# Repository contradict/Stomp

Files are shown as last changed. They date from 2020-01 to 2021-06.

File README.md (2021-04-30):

# Software for the Pneumatic Legged Robot "Chomp"

This repository contains the control software for Chomp the BattleBot.
Presently, Chomp has two separate systems the Hull and the Turret. Each is
entirely self-contained with its own power and control systems. A rough
[schematic](SystemBlockDiagrams) of the Hull is available.

## Hull

The Hull consists of 6 leg modules. Each leg has a control [board](LegBoard) for
local joint coordination. This board uses an STM32F722 microcontroller to
communicate with the joint angle sensors, the Enfield S2 servos, and the central
microcontroller.  This processor measures the joint angles and provides
pneumatic cylinder length feedback as an analog voltage to the servos. Commands
are provided over an RS485 serial connection using the Modbus protocol and can
configure the servos, command a toe position, and provide status information
such as measured leg position and cylinder pressures.

The central microcontroller is a BeagleBone AI running Debian Linux. Two
executables are used during operation
[sbus_radio](Hull/HullControl/src/sbus_radio) reads serial data from a FrSky
receiver and emits a stream of data using [LCM](https://lcm-proj.github.io/).
[leg_control](Hull/HullControl/src/leg_control) listens to these messages and
passes them to a realtime
([SCHED_FIFO](https://man7.org/linux/man-pages/man7/sched.7.html)) thread. This
thread determines the desired toe positions and communicates with the legs over
the RS485 bus.

## Turret

The Turret uses the control electronics from the previous revision of
[Chomp](https://www.github.com/jascahlittle/Chomp). This uses a single Arduino
Mega with an ATMega2560 to switch the pneumatic valves for firing the hammer and
communicate with the control radio, turret rotation motor controller, LeddarTech
M16-LSR, and telemetry radio. There is a nice overview of the control software
[here](Turret/arduino/turret). This software handles the automatic tracking and
hammer firing using the ranging data from the LeddarTech M16-LSR, as well as
precisely scheduling the valve timings to ensure a clean throw and retract of
the hammer.

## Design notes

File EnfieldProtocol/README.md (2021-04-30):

# Enfield S3 Serial Protocol Documentation

## Introduction

This documentation is incomplete and generated by watching the communication
between the Enfield configuration tool and a valve. The USB connection is
converted to serial on the bottom of the two boards inside the servo, I connected
after this conversion as shown here:
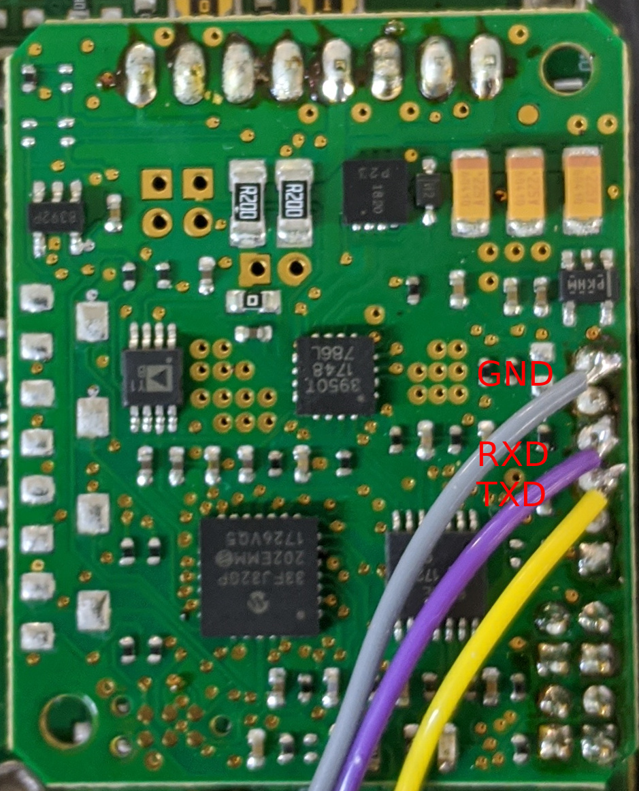
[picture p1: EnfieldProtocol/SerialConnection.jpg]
Serial Connection


To monitor communication, RXD and TXD were each connected to the Receive wire of
another serial port on a second laptop and `twocolumn.py` was used to monitor
the data flow while interacting with the tool. Once the protocol was clear,
`enfield.py` was written to send and receive messages.

## Wiring

In order to use this protocol, we modified our servos to have the following
connections. These colors are the colors in the cables we received from Enfield.

Pin | Color | Function
----------------------
 1  | BRN   | 24V
 2  | WHT   | Feedback Voltage
 3  | BLU   | GND
 4  | BLK   | TXD (data in to Enfield)
 5  | GRY   | RXD (data out of Enfield)

## The Protocol

Packets sent in both directions are fixed size and checksummed. All messages are
checksummed using the `modbus` CRC. Every valid packet produces a response, the
valve never sends an unrequested packet. Baud rate is 115200.

### Commands

Commands are sent to the valve and have the format

    $CrVV#CC

`r` identifies the target of the command and `VV` is a 16-bit payload. `CC` is
the CRC.

### Responses

Responses from the valve have the format

    +VV#CC

The returned 16 bit data is `VV`and the checksum is `CC`

### Observed Reads

The following `r` values return data about the valve and do not seem to affect
its operation. When reading, `VV` in the command packet is always set to 0x1111.
See the manual for a description of what each parameter means.

Name                | `r` |      | Range   | Description
--------------------|-----|------|---------|-------------
ProportionalGain    | 112 | 0x70 | 0-1000  | interpreted as 0-100.0%
DerivativeGain      | 113 | 0x71 | 0-1000  |
ForceDamping        | 119 | 0x77 | 0-1000  |
Offset              | 126 | 0x7E | 0-1000  |
CommandInput        | 127 | 0x7F | 0-1     |
FeedbackInput       | 128 | 0x80 | 0-1     |
AreaRatio           | 129 | 0x81 | 0-32767 | 32767 * (rod end piston area / bore area)
CylinderBore        | 130 | 0x82 | 0-32767 | 1024 * Cylinder Bore in inches
MinimumPosition     | 131 | 0x83 | 0-1000  |
MaximumPosition     | 132 | 0x84 | 0-1000  |
PortConnection      | 133 | 0x85 | 0-1     |
RampUp              | 134 | 0x86 | 0-1000  |
RampDown            | 135 | 0x87 | 0-1000  |
DeadBand            | 137 | 0x88 | 0-1000  |
DitherAmplitude     | 138 | 0x89 | 0-1000  |
ValveOffset         | 139 | 0x8A | 0-1000  |
Unknown             | 140 | 0x8B |         | response is 0x0000
FeedbackPolarity    | 144 | 0x90 | 0-1     |
DigitalCommand      | 145 | 0x91 | 0-4095  |
CommandSource       | 146 | 0x92 | 0-1     |
SerialNumberLo      | 147 | 0x93 |         | response is 0x79db
SerialNumberHi      | 148 | 0x94 |         | response is 0x0000
Unknown             | 149 | 0x95 |         | Only seen as first command, data is 0x2222 response is 0x0000
AnalogCommand       | 152 | 0x98 | 0-4095  | Read continuously by Enfield tool
FeedbackPosition    | 153 | 0x99 | 0-4095  | Read continuously by Enfield tool
BaseEndPressure     | 154 | 0x9A |         |
RodEndPressure      | 155 | 0x9B |         |
SpoolCurrentMeasured| 158 | 0x9E | 0-4096  | Idles at 2048
FirmwareVersionB    | 161 | 0xa1 | 0       | startup, response is 0000
FirmwareVersionA    | 162 | 0xa2 | 0       | startup, response is 0a00
FirmwareRevLow      | 163 | 0xa3 | 0       | startup, response is 3030
FirmwareRevHigh     | 164 | 0xa4 | 0       | startup, response is 4520 "33-0010-0000 E00"
Unknown             | 177 | 0xb1 | 0       | data 0x0000 on Enfield tool startup, response is 0xa00f
Unknown             | 185 | 0xb9 | 0       | data 0x0000 on Enfield tool startup, response is 0x0000

### Observed Writes

These operations change the state of the servo, but are not persisted across
power cycles until `SaveConfiguration` is sent.

Name              | 'r' | Range   | Description
------------------|-----|---------|------------
ProportionalGain  | 1   | 0-1000  |
DerivativeGain    | 2   | 0-1000  |
ForceDamping      | 8   | 0-1000  |
Offset            | 15  | 0-1000  |
CommandInput      | 16  | 0-1     | 0-4-20mA, 1-0-10v
FeedbackInput     | 17  | 0-1     | 0-4-20mA, 1-0-10v
AreaRatio         | 18  | 0-32767 | 32767 * (rod end piston area / bore area)
CylinderBore      | 19  | 0-32767 | 1024 * Cylinder Bore diameter in inches
MinimumPosition   | 20  | 0-1000  |
MaximumPosition   | 21  | 0-1000  |
PortConnection    | 22  | 0-1     | 0-standard, 1-transposed
RampUp            | 23  | 0-1000  |
RampDown          | 24  | 0-1000  |
DeadBand          | 26  | 0-1000  |
DitherAmplitude   | 27  | 0-1000  |
ValveOffset       | 28  | 0-1000  |
FeedbackPolarity  | 33  | 0-1     | 0-normal, 1-inverted
CommandSource     | 89  | 0-1     | 1-analog, 0-slider
DigitalCommand    | 88  | 0-4095  |
SetZeroGains      | 224 | 0       | always written 0 after changing command input type, no response also sent on 'reset to factory'
SaveConfiguration | 225 | 0       | write 0 to save configuration, no response

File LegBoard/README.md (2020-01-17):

# Stomp Leg Board

Each leg of the robot needs a control board to interface to the servos valves
and position sensors. The servos communicate with proprietary serial protocol
and the position sensors measure joint angle which needs to be converted to
cylinder length to use the built-in feedback loop.

## Board Layout

I added a representative connector for each connection this board will need and
picked a pinout. The layout of the connectors is being designed in parallel with
the rest of the leg, hopefully that will be settled soon. The pinout can be
freely changed, please update the Block Diagram schematic if it does.

## Electrical Specifications

## Power

Power is distrubeted from a central power distribution block on the robot
directly from a battery pack. The supplied voltage will be in the 18-28V range.
Each leg board will be supplied through a fuse at the distribution block.

### Enfield S2 servo valve output

| Signal | Description |
|---|---|
| Output Voltage | 24V nominal, the data sheet specs 10-28v |
| Output Current | 1A per valve |
| RXD | 5V TTL asynchronous serial data from servo valve |
| TXD | 5V TTL asynchronous serial data to servo valve |
| Feedback | 0-10V cylinder position measurement |

The feedback signal should have an analog bandwidth of at least 1kHz.

### Angular Position Sensor

| Signal | Description |
|---|---|
| +5V | Power to angle sensor, 10mA |
| Vsense | Measured angle, 0.25 to 4.75 over specified angle range |

The measurement circuit for Vsense should have at least 1kHz bandwidth.

### Communications Bus

The communication bus connects all the Leg Boards to the platform
microcontroller. The two connectors pass through A and B lines to make wiring
simple.

| Signal | Description |
|---|---|
| A | RS-485 A line |
| B | RS-485 B line |
| GND | Reference voltage for RS485 transcievers |
| Upstream | Connected to the Leg Board closer to the microcontroller or the |
| | microcontroller |
| Downstream | Connected to the Leg Board farter from the microcontroller |

I'm not sure how the grounding should work, it may be that ground should not be
wired in the harness on these connetors to avoid a ground loop, but I would like
to provide it in case we have signal integrity problems.

The `Upstream` and `Downstream` pins should each be connected to a processor
GPIO pin.  I would like to use them to avoid having to hard code addresses on
each board.

## Signal Processing

Since the position sensors we are installing measure angle and the servo valves
need to know cylinder length, each channela $i$  needs to calculate

```math
\theta_i =  as_i * (V_{sense} + ao_i)
l_{cylinder} = a_i + b_i \cos(\theta_i + \phi_i )
V_{feedback} = fo_i + fs_i * l_{cylinder}
```

Where $as_i$ and $ao_i$ define the conversion from sensor voltage to angle in
radians, $a_i$, $b_i$, and $phi_i$ define the geometry of the link, and $fo_i$
and $fs_i$ define the conversion from cylinder length back to voltage.

This calculation should take at most 20us per channel to ensure low latency and
CPU usage for the full calculation. This should not be hard for a
microcontroller with a clock rate of at least 50MHz.

## Communications Protocols

### Enfield S2

The processor will need to implement a serial port interface to the
Enfield S2 for delivering command positions and monitoring status. The
reverse-engineered protocol is described in the
[README](../../EnfieldProtocol/README.md). 

The pressure and feedback registers should be continously monitored while
sending the current position command.

### Leg Bus (RS-485)

The commnuication between the Platform microcontroller and the Leg Controllers
over the RS-485 bus should implement the MODBUS protocol.

TODO: MODBUS Register Map.

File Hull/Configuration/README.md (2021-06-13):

# BeagleBone AI setup notes

Comes from TI with account `debian:tempwd`, hostname beaglebone.

## Set debian password

    ssh debian@beaglebone
    passwd

## Packages

    sudo apt update && sudo apt upgrade
    sudo apt install gdb stow cmake \
        liblcm-dev liblcm-bin libglib2.0-dev \
        libtool-bin libbsd-dev \
        openjdk-8-jre libjchart2d-java liblcm-java

## Upgrade scripts

Must use `debian` account. Copied from [here](https://beagleboard.org/upgrade)

    cd /opt/scripts
    git pull
    sudo tools/update_kernel.sh

## Set hostname

The preferred hostname is `chomp-hull`

    sudo vim /etc/hostname

## User Account for developers

    sudo adduser <username>
    GRPS=$(groups | cut -d ' ' -f 2- | tr ' ' ',')
    sudo usermod -a -G $GRPS <username>

## Account for robot operation

    sudo adduser chomp
    GRPS=$(groups | cut -d ' ' -f 2- | tr ' ' ',')
    sudo usermod -a -G $GRPS <username>

## disable USB networking (don't need it, adds noise to the logs)

In `/etc/default/bb-boot`, add the line (or uncomment)

    USB_NETWORK_DISABLED=yes

In `/etc/network/interfaces`, comment out the whole `iface usb0` section.

In `/opt/scripts/boot/bbai.sh`, comment out the two blocks starting around line
368 that run `autocnifgure_usb[01].sh`.

## Ensure a multicast route always exists.
If LCM won't start at boot, this is probably the solution.

Add these two `post-up` lines to `/etc/network/interfaces`. The reset should
already be there:

    auto lo
    iface lo inet loopback
      post-up ifconfig lo multicast || true
      post-up route add -net 224.0.0.0 netmask 240.0.0.0 dev lo || true

## Reboot

If the kernel was upgraded above, a reboot is necessary before building the
devicetree overlays.

## Use new account

Unless you reboot, still has `beaglebone` hostname.

    exit
    ssh-copy-id <username>@beaglebone

Enter password, then ssh in with keys.

## Custom Devicetree

Builds custom device tree overlays for UART3, UART5, UART10, SPI3, ADC, and I2C
IMU. This should use your developer account.

    cd ~
    mkdir src
    cd src
    git clone git@github.com:contradict/BeagleBoard-DeviceTrees
    cd BeagleBoard-DeviceTrees
    git checkout -b chomp
    make

This command creates the file

    src/arm/BBAI-chompcape.dtb

Need to copy the file to `/lib/firmware/`

    sudo cp src/arm/BBAI-*.dtb /lib/firmware

## Config files

`uEnv.txt` needs to be updated, the lines at the end installing the DTB overlays
are the important part, be sure not to overwrite any kernel version parameters
earlier in the file.

    90-mikrobus-cape.rules -> /etc/udev/rules.d/

## Reboot

Again. To use the new dtb overlays.

    sudo reboot

## Fetch and build libmodbus

The version in the debian repositories is old and busted. The version from the
official libmodbus site works, but is missing diagnostics. For our branch with a
minimal diagnostics client, use this:

    cd src
    git clone -b diagnostics_client https://github.com/contradict/libmodbus
    cd libmodbus
    ./autogen.sh
    ./configure --prefix=/usr/local/
    make
    sudo make install DESTDIR=/usr/local/stow/libmodbus-diag
    sudo mv /usr/local/stow/libmodbus-diag/usr/local/* /usr/local/stow/libmodbus-diag
    sudo rm -r /usr/local/stow/libmodbus-diag/usr
    sudo stow -d /usr/local/stow libmodbus-diag

## Fetch and build project

    cd src
    git clone git@github.com:contradict/Stomp
    cd Stomp/Platform
    make -C Test
    make -C SimpleGait

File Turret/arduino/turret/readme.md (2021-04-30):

# Table Of Contents <!-- omit in toc --> #

- [Design Overview](#design-overview)
- [Controller Hierarchy](#controller-hierarchy)
- [Main Program (turret.ino)](#main-program-turretino)
- [State Machine Pattern](#state-machine-pattern)
- [Controller Pattern](#controller-pattern)
- [Notes about changes to original Chomp code](#notes-about-changes-to-original-chomp-code)

# Design Overview #

Most logic is implemented c++ classes that use the Chomp controller pattern ([see below](#controller-pattern)).  Each controller implements a state machine ([see state machine pattern below](#state-machine-pattern)).

There are 4 global controllers

- Turret Controller
- Target Tracking Controller
- Radio Controller
- Telemetry Controller

Each of these are a global instances and they are all declared in turret.ino.  Then an <code>extern</code> deceleration is provided in each of those controller's class header file.

The Turret Controller and the TargetTrackingController will consturct new private instances of the controller types they need to do thier job.  However, each of these private controllers are owned by a global controller, which should not expose access to those controllers.

# Controller Hierarchy #

The current controller hierachy looks like this

    Global Objects                Sub Objects (instantiated in global object init())
    --------------                --------------------------------------------------

    TurretController -------------+--- TurretRotationController --------+--- AutoAimController
                                  |
                                  +--- HammerController
                                  |
                                  +--- FlameThrowerController
                                  |
                                  +--- IMUController
                                  |
                                  + --- AutoFireController

    TargetTrackingController -----+--- TargetAcquisitionController ------+--- LeddarController

    RadioController

    TelemetryController

# Main Program (turret.ino) #

The main Arduino file is turret.ino.  This file is where the 4 global controllers are declared.

    TurretController Turret;
    TargetTrackingController TargetTracking;
    RadioController Radio;
    TelemetryController Telem;

In the <code>setup()</code> method, that is called when the Arduino is (re)started, the <code>Init()</code> method of the 4 global controllers is called to get everything started.  Then the <code>RestoreParas()</code> call is issed to the global controllers

    void setup()
    {
        Telem.Init();
        Radio.Init();
        TargetTracking.Init();
        Turret.Init();

        Telem.RestoreParams();
        TargetTracking.RestoreParams();
        Turret.RestoreParams();
    }

Then each update that the Arduino issues by calling <code>loop()</code> will call the <code>Update()</code> method on each of the 4 global controllers.

    void loop()
    {
        Radio.Update();
        TargetTracking.Update();
        Turret.Update();
        Telem.Update();
    }

# State Machine Pattern #

Each controller will define its states in an <code>enum</code> in the header file.  For example this is what the flameThrowerController defines:

    enum controllerState 
    {
        EInit,
        ESafe,
        
        EDisabled,
        EReadyToFire,

        EPulseFlameOn,
        EManualFlameOn,
 
        EInvalid = -1
    };

The state machine pattern used by all controllers basically consists of code in the main <code>Init()</code> method, the <code>Update()</code> method and a private <code>setState(controllerState p_state)</code> method.

The <code>Init()</code> method will ensure the state is set and initialize the <code>m_lastUpdateTime</code> private member variable.  Finally, the state will be set to the initial state, which should be name <code>EInit</code>.  All other initilization should happen in the code triggered by transitioning into the <code>EInit</code> state.

    void FlameThrowerController::Init()
    {
        m_state = EInvalid;    
        m_lastUpdateTime = micros();

        setState(EInit);
    }

The <code>Update()</code> will first do any update calculations needed to detect state transitions, then the current state of the controller is stablized by running through all valid state transitions.  Once the state has stablized, then any other update code can run.

    void FlameThrowerController::Update()
    {
        m_lastUpdateTime = micros();

        //  Do any processing necessary for being able to detect state transitions

        ...

        //  Stabilize our state

        while(true)
        {
            controllerState prevState = m_state;

            switch (m_state)
            {
                case EInit:
                {
                    setState(ESafe);
                }
                break;

                case ESafe:
                {
                    //  Stay in safe mode for a minimum of k_safeStateMinDt

                    if (m_lastUpdateTime - m_stateStartTime > k_safeStateMinDt && Radio.IsNominal())
                    {
                        setState(EDisabled);
                    }
                }
                break;

                case EDisabled:
                {
                    if (!Radio.IsNominal())
                    {
                        setState(ESafe);
                    }
                    else if (Radio.IsFlameEnabled() || Radio.IsFlamePulseEnabled())
                    {
                        setState(EReadyToFire);
                    }
                }
                break;

                ...

                default:
                break;
            }

            //  No more state changes, move on
            
            if (m_state == prevState)
            {
                break;
            }
        }

        //  Now that the state is stable, perform any other update processing

        ...
    }

# Controller Pattern #

# LEDDAR Processing Overview #

The [LEDDAR M16](https://leddartech.com/lidar/m16-multi-segment-sensor-module/)
produces 16 range measurements spread over a 48° horizontal by 3° vertical fan.
It is possible for each measurement to return multiple reflections, we accept
the one closest to the robot in each segment. The list of measurements is scanned,
looking for features that project radially inwards toward the robot, with some
careful handling of [edge
cases](https://github.com/contradict/Stomp/blob/f4baf6cf64f448c69cff76d400e4cbb2790b86ec/Turret/arduino/turret/targetAcquisitionController.cpp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).
These segmentations are then compared to the current state of an
[$\alpha-\beta$](https://en.wikipedia.org/wiki/Alpha_beta_filter)
[filter](https://github.com/contradict/Stomp/blob/master/Turret/arduino/turret/targetTrackingController.cpp)
and the closest one is used to update the filter state. The rules around
initialization and target loss are fiddly, but seem to cope with occasional
sensor noise relatively well.

The tracked target is the used for two tasks. The first is keeping the turret
pointed at the tracked
[target](controlle://github.com/contradict/Stomp/blob/master/Turret/arduino/turret/autoAimController.cpp).
This uses a PID loop providing a velocity command to the turret rotation motor
to keep the tracked target at the center of the field of view.

If auto-swing is enabled, the tracked target is also used to predict when to
fire the
[hammer](https://github.com/contradict/Stomp/blob/master/Turret/arduino/turret/autoFireController.cpp)
Using the IMU measured rotation speed of the turret and the estimated velocity
of the target, the position of the target relative to the turret is estimated at
a time in the future corresponding to the hammer swing duration. If the hammer
and the target are expected to arrive at the sample place and time, the hammer
is automatically triggered.

# Notes about changes to original Chomp code #

Files that were just removed because they were no longer necessary

- autodrive.cpp
- drive.cpp
- hold_down.cpp
- rc_pwm.cpp
- selfright.cpp
- telem_message_stream.h

Files that had there contents become a contoller object

    New File                                Old File
    ------------------------------          ------------------------------
    turretController.cpp                    chomp_main.cpp
    autoFireController.cpp                  autofire.cpp
    autoAimController.cpp                   autoaim.cpp
    radioController.cpp                     sbus.cpp
    telemetryController.cpp                 telem.cpp & xbee.cpp
    imuController.cpp                       imu.cpp
    leddarController.cpp                    leddar_io.cpp
    target.cpp                              object.cpp
    targetTrackingController.cpp            track.cpp
    targetAcquisitionController.cpp         targeting.cpp

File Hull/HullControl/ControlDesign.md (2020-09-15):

# Notes concerning design of Hull remote control software

## Leg Control Process

This process is responsible for communication with the leg microcontrollers and
computing the leg positions.

```
  thread 1 (real-time scheduler, 100Hz)
    Odd loops
      parameters = read parameter queue
      X, Y, Z = compute leg position ( parameters )
      Send Leg positions (X, Y, Z)
    even loops
      data = Read position, pressure from each leg
      Queue data in telemetry queue
      if command in command queue
        send to hardware
        Queue response in response queue
  thread 0 (main, running lcm)
    Multiplexed by LCM, topic callbacks for
        receive messages from control topic, compute parameters, enqueue to parameters queue
        Receive commands from topic, queue to real-time command queue
    Receive responses from response queue, send to response topic
    Receive data from telemetry queue, send to telemetry topic
```

### Leg position generation, interpolated gait

This is the `compute leg position` subroutine mentioned above.

```
    Inputs: forward velocity V, curvature \kappa, interval \delta t
    State: phase
    Constants: Step shape, robot half-width W
    Each call
        compute frequency that results in full length step for legs on fastest side
            V_left = V * (1 - W * \kappa)
            V_right = V * (1 + W * \kappa)
            V_max = signed_max(V_left, V_right) 
            \omega = V_max / max_step_length
        compute step scale
            \alpha[left legs] = V_left / V_max
            \alpha[right legs] = V_right / V_max
        advance phase
            \phi += \omega * \delta t
        compute scaled leg positions from step shape
            for each leg l
                X[l], Y[l], Z[l] = step_shape(\phi + \leg_offset[l])
                Y[l] *= \alpha[l]
    return X, Y, Z
```

## Control radio process

Read from S.BUS serial port and produce messages for the rest of the system.

```
  forever
    Read packet from radio
    parse to axes and switches
    send to control topic
```

## Telemetry COSMOS interface

Translate internal LCM messages to COSMOS, bidirectional.

```
  Poll loop with serial port, topic file descriptors:
      forward received packets to command topic
      Forward response topic to radio
      forward telemetry topic to radio
```

## Others

 * IMU Data?
 * Pressure sensors

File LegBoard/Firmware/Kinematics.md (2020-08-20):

# Linearization of feedback

The Enfield servos need cylinder length feedback, our systems measures joint
angles on a four-bar linkage.

## Definition of Symbols

Values measured during operation.

| Measurement  | Description |
|---|---|
| $\theta_l$ | Measured by Lift angle sensor |
| $\theta_c$ | Measured by Curl angle sensor |
| $\theta_s$ | Measured by Swing angle sensor |

Parameters determined by leg geometry.

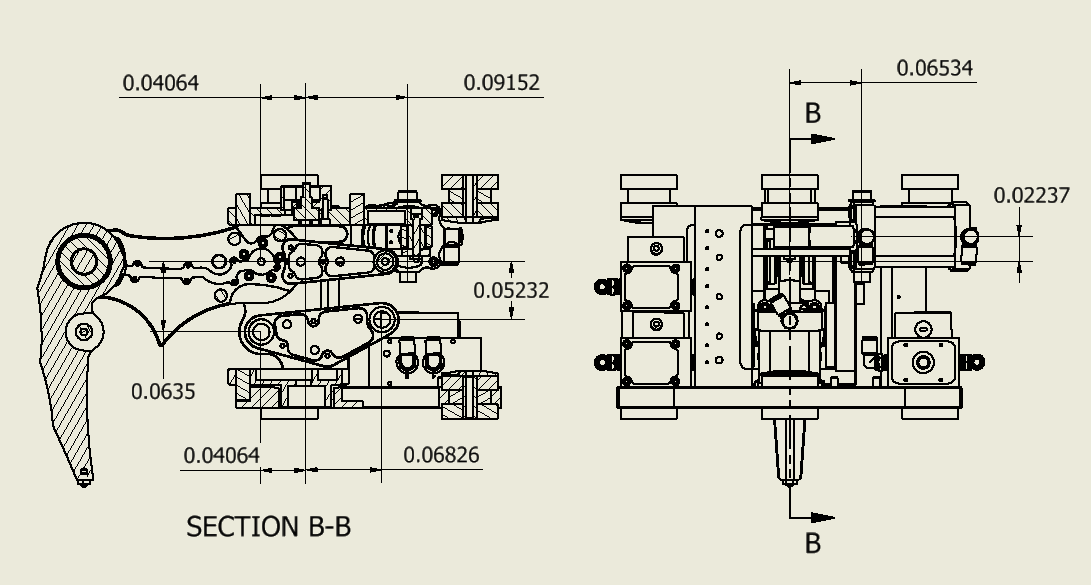
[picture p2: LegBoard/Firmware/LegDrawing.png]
Mechanical Drawing


| Parameter | Value (m) | Description |
|---|---|---
| $(l_x, l_y)$ | $( 0.04064,  0.00000)$ | Position of Lift Link Pivot relative to Swing Pivot |
| $(L_x, L_y)$ | $(-0.06826, -0.05232)$ | Position of Lift Cylinder Pivot relative to Swing Pivot |
| $(C_x, C_y)$ | $( 0.04064, -0.06350)$ | Position of Curl Cylinder Pivot relative to Swing Pivot |
| $L_1$ | $0.11176$  | Length of link from Lift Cylinder Rod End to Lift Cylinder Pivot |
| $L_2$ | $0.16002$  | Length of link from Lift Cylinder Pivot to Curl Link Pivot |
| $C_4$ | $0.0635$ | Distance from Curl Cylinder Pivot to Lift Link Pivot |
| $C_1$ | $0.0635$ | Length of link from Curl Link Pivot to Curl Cylinder Rod End |
| $C_2$ | $0.2032$ | Length of Curl Link |
| $S_1$ | $0.09906$ | Length of link from Swing Cylinder Rod End to Swing Cylinder Pivot |
| $S_3$ | $0.112458$ | Length of link from Swing Cylinder Pivot to Swing Link Pivot |
| $(S_x, S_y)$ | $(-0.09152, -0.06534)$ | Position of Swing Cylinder Pivot relative to Swing Pivot|
| $R_c^{\textrm{min}}$ | $0.14732$ | Minimum distance from Curl Cylinder Pivot to Curl Cylinder Rod End |
| $R_c^{\textrm{max}}$ | $0.17272$ | Maximum distance from Curl Cylinder Pivot to Curl Cylinder Rod End |
| $R_l^{\textrm{min}}$ | $0.027178$ | Minimum distance from Lift Cylinder Pivot to Lift Cylinder Rod End |
| $R_l^{\textrm{max}}$ | $0.07747$ | Maximum distance from Lift Cylinder Pivot to Lift Cylinder Rod End |
| $R_s^{\textrm{min}}$ | $0.027432$ | Minimum distance from Swing Cylinder Pivot to Swing Cylinder Rod End |
| $R_s^{\textrm{max}}$ | $0.0653288$ | Maximum distance from Swing Cylinder Pivot to Swing Cylinder Rod End |

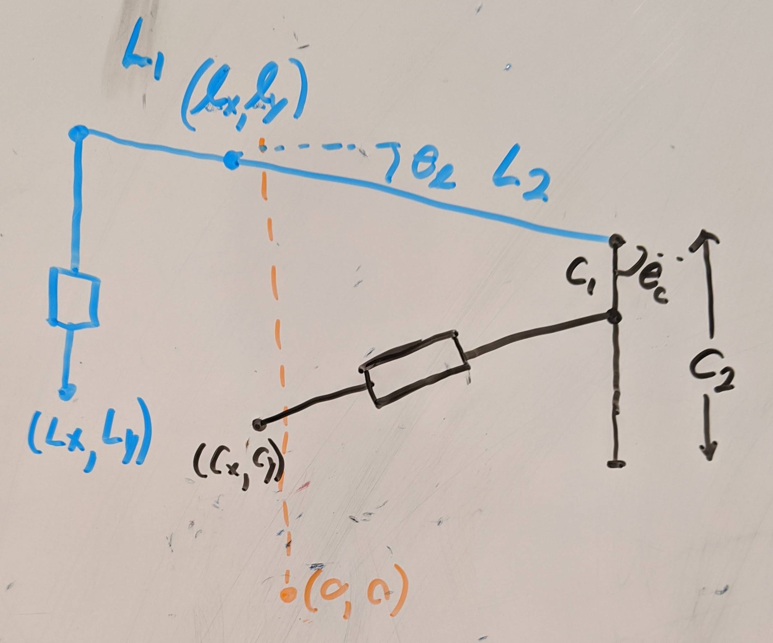
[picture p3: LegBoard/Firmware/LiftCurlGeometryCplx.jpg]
Sketch of Leg Geometry


## Solve with complex variables

The lift cylinder loop is

$$ L + R_l e^{i \alpha_l} + L_1 e^{i \theta_l} = l $$
$$ R_l e^{i \alpha_l} = l - L - L_1 e^{i \theta_l} $$
$$ R_l = \left\| l - L - L_1 e^{i \theta_l} \right\| $$

The curl cylinder loop is

$$ C + R_c e^{i \alpha_c} - C_1 e^{i (\theta_c + \theta_l)} - L_2 e^{i \theta_l} \
   = l $$

$$ R_c e^{i \alpha_c} = l - C + C_1 e^{i (\theta_c + \theta_l)} + L_2 e^{i \theta_l} $$
$$ R_c = \left\| l - C + C_1 e^{i (\theta_c + \theta_l)} + L_2 e^{i \theta_l} \right\| $$

The swing loop is

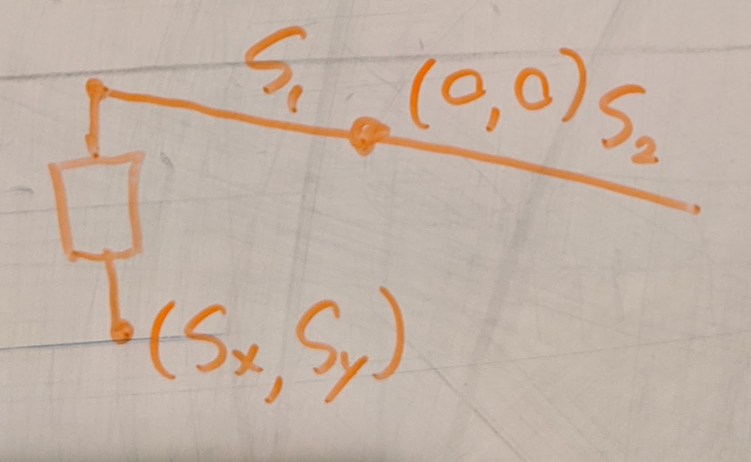
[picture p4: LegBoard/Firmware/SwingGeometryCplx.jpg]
Sketch of Swing Geometry


$$ S + R_s e^{i \alpha_s} + S_1 e^{i \theta_s} = 0 $$

$$ R_s = \left\|-S - S_1 e^{i \theta_s}\right\| $$

# Toe position to cylinder lengths

The previous result gives cylinder lengths in terms of join angles, so just
solve for joint angles in terms of toe position.

Toe position in terms of joint angles

$$ l + L_2 e^{i \theta_l} + C_2 e^{i (\theta_l + \theta_c)} = T $$

First isolate and solve for $\theta_c$

$$ L_2 e^{i \theta_l} + C_2 e^{i (\theta_l + \theta_c)} = T - l $$
$$ e^{i \theta_l} (L_2 + C_2 e^{i \theta_c}) = T - l $$
$$ \|L_2 + C_2 e^{i \theta_c}\| = \|T - l\| $$
$$ (L_2 + C_2 \cos(\theta_c))^2 + C_2^2 \sin^2(\theta_c) = \|T - l\|^2 $$
$$ L_2^2 + 2 L_2 C_2 \cos(\theta_c) + C_2^2 \cos^2(\theta_c) + C_2^2 (1-\cos^2(\theta_c)) = \|T - l\|^2 $$
$$ L_2^2 + 2 L_2 C_2 \cos(\theta_c) + C_2^2 = \|T - l\|^2 $$
$$ 2 L_2 C_2 \cos(\theta_c) C_2^2 = \|T - l\|^2 - (L_2^2 + C_2^2) $$
$$ \theta_c = \pm \arccos\left(\frac{\|T - l\|^2 - (L_2^2 + C_2^2)}{2 L_2 C_2}\right) $$

The positive branch is not physical, use the negative one.

Solve for $\theta_l$

$$ e^{i \theta_l} = \frac{T - l}{L_2 + C_2 e^{i \theta_c}}$$
$$ \theta_l = \
\arcsin\left(\Im\left(\frac{T - l}{L_2 + C_2 e^{i \theta_c}}\right)\right)$$

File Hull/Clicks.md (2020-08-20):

## Click1 - IMU / Telemetry Radio
  * Telemetry UART uart3 ttyS2
     * RXD  P9.22
     * TXD  P9.21
  * IMU SPI spi3
    * MISO P9.29
    * MOSI P9.30
    * SCK  P9.31
    * CS   P9.28 spi3_cs0
  * IMU I2C i2c4
    * SCL  P9.19
    * SDA  P9.20

## Click2 - ADC
  * ADC SPI spi3
    * MISO P9.29
    * MOSI P9.30
    * SCK  P9.31
    * CS   P9.42 spi3_cs1

## Click3 - Control Radio
  * Control UART uart10 ttyS1
    * RXD  P9.26
    * TXD  P9.24

## Click4 - RS485
  * RS485 UART uart5 ttyS4
    * RXD  P9.11
    * TXD  P9.13
    * DE   P8.06

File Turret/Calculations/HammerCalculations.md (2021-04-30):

# Hammer operation

The pneumatic hammer makes efficient use of air by allowing an initial charge of
air to expand during the throw phase. The initial charge is metered by opening
the fill valve on command and closing it once the hammer has passed a specified
angle, or by leaving the valve open for a maximum time.

** Hammer throw energy calculations here **

## Braking

During the retract phase, the same techniques is used in the retract cylinder.
To prevent the hammer from colliding with its stop, the hammer is decelerated by
compressing air in the throw cylinder. 

The energy that can be absorbed by the throw cylinder to brake the retract
motion between the angle of initial braking $\bar{\theta}$ and final
stopping angle of $\theta_s$ is

$$E_{brake} = -\int_{\bar{\theta}}^{\theta_s} P(\theta) dV(\theta)$$

Making a simplifying (and incorrect) assumption that the process is isothermal

$$P(\theta) = \frac{P_{atm} V(\bar{\theta})}{V(\theta)}$$

The volume of the throw cylinder is linear in throw angle as the throw chain
wraps around its sprocket at $p_r$.

$$V(\theta) = \pi r_{throw}^2 p_r \theta$$

Solving

$$E_{brake} = -\int_{ \bar{\theta}}^{\theta_s}
\frac{P_{atm} \pi r_{throw}^2 p_r \bar{\theta}}{\pi r_{throw}^2 p_r \theta}
\pi r_{throw}^2 p_r d\theta$$

$$E_{brake} = -P_{atm} \pi r_{throw}^2 p_r \bar{\theta}
\int_{ \bar{\theta}}^{\theta_s}
\frac{d\theta}{\theta} $$

$$E_{brake} = -P_{atm} \pi r_{throw}^2 p_r \bar{\theta}
(\ln{\theta_s} - \ln{\bar{\theta}})$$

$$E_{brake} = P_{atm} \pi r_{throw}^2 p_r \bar{\theta}
\ln{\frac{\bar{\theta}}{\theta_s}}$$

Close the vent valve when the hammer energy becomes greater than the braking
energy with a suitable stopping angle $\theta_s$.

$$\frac{1}{2} I \omega^2 \geq E_{brake}$$

$$\frac{1}{2} I \omega^2 \geq P_{atm} \pi r_{throw}^2 p_r \theta
\ln{\frac{\theta}{\theta_s}}$$

| Description | Parameter | Value  | Units |
|---|---|---|---|
| Atmospheric Pressure | $P_{atm}$ | 101325 | $Pa$ |
| Hammer Moment of Inertia | $I$ | 1.818  | $kg\,m^2$ |
| Throw Cylinder Radius | $r_{throw}$ | 0.0762 | $m$ |
| Throw Sprocket Pitch Radius | $p_r$ | 0.0964 | $m$ |
| Hammer Angle | $\theta$ | | $rad$ |
| Hammer Brake Angle | $\bar{\theta}$ | | $rad$ |
| Hammer Stop Angle | $\theta_s$ | 0.0873 | $rad$ |

I think the efficient way to evaluate the braking condition is

$$\frac{\frac{1}{2} I}{P_{atm} \pi r_{throw}^2 p_r } \omega^2 \geq
\theta \ln{\frac{\theta}{\theta_s}}$$

Checking units.

$$\frac{[kg][m]^2}{[kg][m]^{-1}[s]^{-2}[m]^2[m]} = [s]^2$$

Numerically

$$ 5.102e-3 \omega^2 \geq \theta \ln{\frac{\theta}{\theta_s}}$$

## Sensor calibration.

### ADC Converter

The ADC uses a $V_{ref}5V$ reference and makes a $n=10$ bit conversion. This means an ADC
code of $c$ gives

$$V(c) = \frac{c * V_{ref}}{2^n}=\frac{c * 5}{1024}$$

A convenient scale for representing voltage in a 16bit signed value is $mV$,
calculated as

$$V(c) = c*4 + c*\frac{22}{25}$$

### Hammer Angle

The voltage from the hammer angle sensor should always be $0.5V \leq v \leq 4.5V$,
voltages outside this range indicate a disconnected or damaged sensor.

The hammer angle sensor reads $v_{min}=4.004V$ at $\theta=0$ and $v_{max}=1.941V$
at $\theta=\pi$.

Symbolically

$$\theta(v) = \frac{v-v_{min}}{v_{max} - v_{min}} \pi$$

With the values measured from our current assembly

$$\theta(v) = (4.004 - v) * 6.481$$

When stored as a 16-bit signed value as scaled from ADC counts, this can be
scaled to miliradians

$$\theta(c) = (820 - c) * 37 / 5 + (820-c)*2/100$$

### Pressure Sensors

The pressure sensor on both cylinders is an SSI Technologies
[P51-500-A-B-I36-4.5V](https://www.ssi-sensors.com/perch/resources/documents/p51-pressure-sensor-p51-ds.pdf).

The pressure sensor voltages should always be $0.5V \leq v \leq 4.5V$,
voltages outside this range indicate a disconnected or damaged sensor.

This sensor has a $P_{max}=500PSIA=3.447e6Pa$ full-scale reading at
$v_{max}=4.5V$ and a voltage of $v_{min}=0.5V$ at $P_{min}=0$ absolute pressure.

The absolute pressure is

$$P(v) = \frac{(v-v_{min})(P_{max} - P_{min})}{v_{max} - v_{min}} + P_{min}$$

In $Pa$,

$$P(v) = (v-0.5) * 8.618e5$$

When stored in a 16 bit signed value, this can be scaled to $kPa$ as scaled from
ADC counts

$$P(c) = (c-102) * 24 / 5$$

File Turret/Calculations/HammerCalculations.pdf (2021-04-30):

## Hammer operation

The pneumatic hammer makes efficient use of air by allowing an initial charge of air to expand during the throw phase. The initial charge is metered by opening the fill valve on command and closing it once the hammer has passed a specified angle, or by leaving the valve open for a maximum time.

** Hammer throw energy calculations here **

Braking

During the retract phase, the same techniques is used in the retract cylinder. To prevent the hammer from colliding with its stop, the hammer is decelerated by compressing air in the throw cylinder.

The energy that can be absorbed by the throw cylinder to brake the retract motion between the angle of initial braking ¯θ and final stopping angle of θs is

Ebrake = −

# Z θs

θ¯

P(θ)dV (θ)

Making a simplifying (and incorrect) assumption that the process is isothermal

P(θ) = PatmV (

¯θ)
V (θ)

The volume of the throw cylinder is linear in throw angle as the throw chain wraps around its sprocket at pr.

V (θ) = πr²
throwprθ

Solving

Ebrake = −

# Z θs

θ¯

Patmπr²
throwpr

¯θ
πr²
throwprθ

πr²
throwprdθ

Ebrake = −Patmπr²
throwpr

¯θ

# Z θs

θ¯

dθ
θ

Ebrake = −Patmπr²
throwpr

¯θ(ln θs − ln ¯θ)

Ebrake = Patmπr²
throwpr

¯θ ln

¯θ

θs

1

Close the vent valve when the hammer energy becomes greater than the braking energy with a suitable stopping angle θs.

1
2

Iω² ≥ Ebrake

1
2

Iω² ≥ Patmπr²

throwprθ ln θ
θs
Description | Parameter | Value | Units
Atmospheric Pressure | Patm | 101325 | P a
Hammer Moment of Inertia | I | 1.818 | kg m²
Throw Cylinder Radius | rthrow | 0.0762 | m
Throw Sprocket Pitch Radius | pr | 0.0964 | m
Hammer Angle | θ | | rad
Hammer Brake Angle | ¯θ | | rad
Hammer Stop Angle | θs | 0.0873 | rad

I think the efficient way to evaluate the braking condition is

1/2 I
Patmπr²
throwpr

ω

2 ≥ θ ln θ
θs

Checking units.

[kg][m]

2
[kg][m]⁻¹[s]⁻²[m]
2[m]

= [s]

2

Numerically

5.102e − 3ω

2 ≥ θ ln θ
θs

Sensor calibration.

ADC Converter

The ADC uses a Vref 5V reference and makes a n = 10 bit conversion. This means an ADC code of c gives

V (c) = c ∗ Vref
2

n

=

c ∗ 5
1024

2

A convenient scale for representing voltage in a 16bit signed value is mV , calculated as

V (c) = c ∗ 4 + c ∗

22
25

Hammer Angle

The voltage from the hammer angle sensor should always be 0.5V ≤ v ≤ 4.5V , voltages outside this range indicate a disconnected or damaged sensor.

The hammer angle sensor reads vmin = 4.004V at θ = 0 and vmax = 1.941V at θ = π.

Symbolically

θ(v) = v − vmin vmax − vmin
π

With the values measured from our current assembly

θ(v) = (4.004 − v) ∗ 6.481

When stored as a 16-bit signed value as scaled from ADC counts, this can be scaled to miliradians

θ(c) = (820 − c) ∗ 37/5 + (820 − c) ∗ 2/100

Pressure Sensors

The pressure sensor on both cylinders is an SSI Technologies P51-500-A-B-I36-4.5V. (https://www.ssi-sensors.com/perch/resources/documents/p51-pressure-sensor-p51-ds.pdf)

The pressure sensor voltages should always be 0.5V ≤ v ≤ 4.5V , voltages outside this range indicate a disconnected or damaged sensor.

This sensor has a Pmax = 500P SIA = 3.447e6P a full-scale reading at vmax = 4.5V and a voltage of vmin = 0.5V at Pmin = 0 absolute pressure.

The absolute pressure is

P(v) = (v − vmin)(Pmax − Pmin)

vmax − vmin

+ Pmin

In P a,

3

P(v) = (v − 0.5) ∗ 8.618e5

When stored in a 16 bit signed value, this can be scaled to kP a as scaled from ADC counts

P(c) = (c − 102) ∗ 24/5

4

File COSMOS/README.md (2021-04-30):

# COSMOS

Ball Aerospace [COSMOS](https://cosmosrb.com/) is the tool we use for telemetry
dashboards. The version we use is modified with some additional plotting
capabilities and can be downloaded [here](https://github.com/contradict/COSMOS).

## Installation

* Install some build dependencies
```bash
$ sudo apt-get install -y build-essential libssl-dev libreadline-dev zlib1g-dev libqt4-dev cmake libpq-dev
```
* Install [rbenv](https://github.com/rbenv/rbenv#basic-github-checkout)

```bash
$ git clone https://github.com/rbenv/rbenv.git ~/.rbenv
$ cd ~/.rbenv && src/configure && make -C src && cd -
```

* Add `rbenv` to your `~/.bashrc` to ensure it is loaded every login. Add these
    two lines somewhere in `~/.bashrc`

```bash
export PATH="~/.rbenv/bin":$PATH
eval "$(rbenv init -)"
```

* Add rbenv to your current path and run `~/.rbenv/bin/rbenv init` to enable
    rbenv in your current environment. Alternatively, open a new shell and the
    lines added to `~/.bashrc` should do the same thing.

```bash
$ export PATH=~/.rbenv/bin:${PATH}
$ eval "$(rbenv init -)"
```

* Install [ruby-build](https://github.com/rbenv/ruby-build#installation), which provides the rbenv install command that simplifies the process of installing new Ruby versions.

```bash
$ mkdir -p "$(rbenv root)"/plugins
$ git clone https://github.com/rbenv/ruby-build.git "$(rbenv root)"/plugins/ruby-build
```

* build ruby 2.5.8

```bash
$ rbenv install 2.5.8
```

* Ensure you are currently in the `Stomp/COSMOS` directory and activate ruby 2.5.8

```bash
Stomp/COSMOS $ rbenv local 2.5.8
```

* install bundler (still in `Chomp/COSMOS` directory)

```bash
Stomp/COSMOS $ gem install bundler
```

* Install this package (still in `Chomp/COSMOS` directory)

```bash
Stomp/COSMOS $ bundle install
```

* run `ruby ./Launcher` in this directory to start COSMOS

```bash
Stomp/COSMOS $ ruby ./Launcher
```

## Development on the custom fork of COSMOS

There is much I still don't understand about how to do this correctly. The above
instructions for installing `ruby 2.5.8` are a good start.

* Our fork is stored [here](https://github.com/contradict/COSMOS)

* After cloning, I did

```bash
~/src/COSMOS $ rbenv local 2.5.8      # Configure this directory with ruby 2.5.8
~/src/COSMOS $ bundle install         # Install development dependencies
~/src/COSMOS $ bundle exec rake build # Build the compiled parts
```
* Run the application with `bundle exec ruby demo/Launcher` to run the app in
  the demo project.

* run `bundle exec rake` to execute the tests

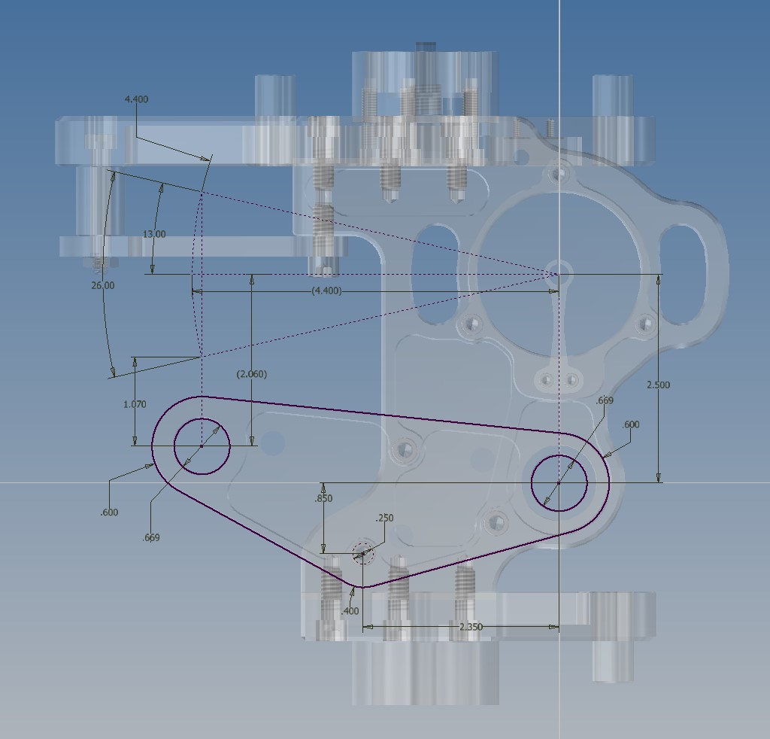
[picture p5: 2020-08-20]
Hull/Drawings/Lift Sketch.jpg

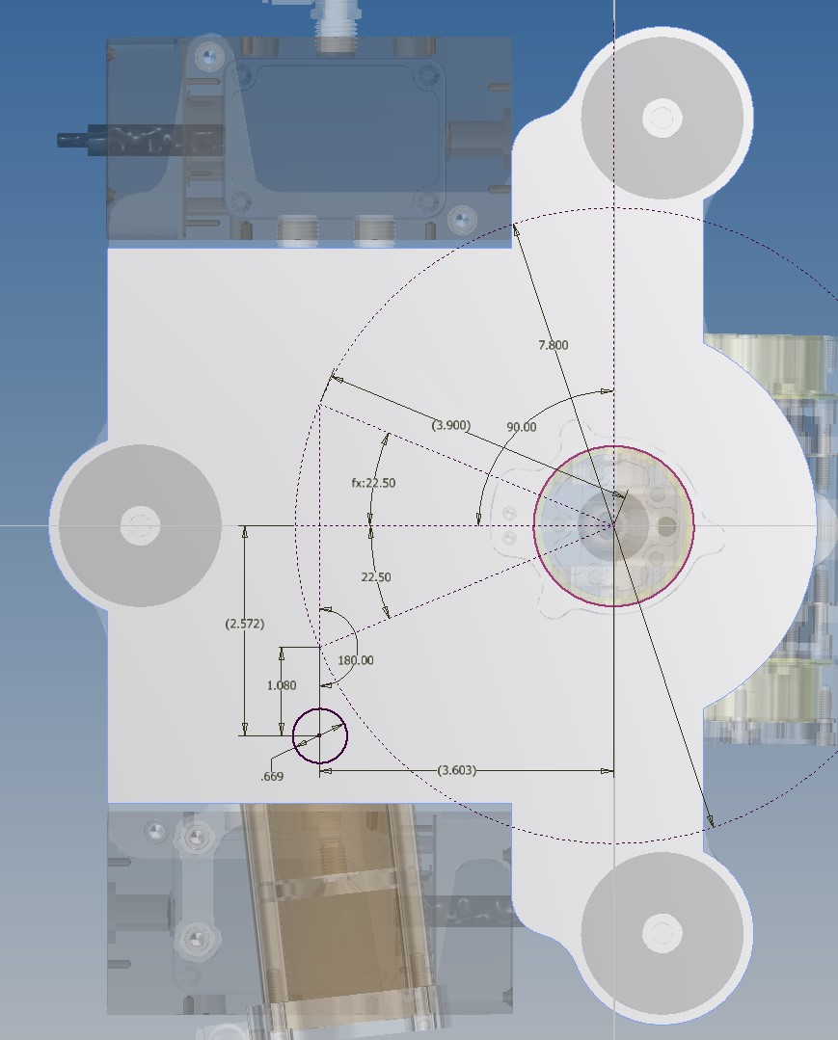
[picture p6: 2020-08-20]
Hull/Drawings/Swing Sketch.jpg

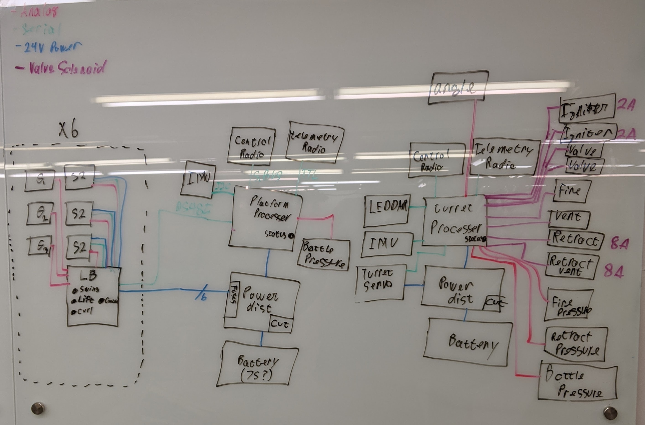
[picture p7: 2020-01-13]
SystemBlockDiagrams/WhiteboardSketch.jpg

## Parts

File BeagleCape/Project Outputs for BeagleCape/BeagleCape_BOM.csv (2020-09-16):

Quantity | Vendor Part Number | DNP | Designator
1 | 296-21805-1-ND |  | U3
1 | 296-49460-1-ND |  | U9
1 | 296-50395-1-ND |  | U1
1 | Archer + |  | U4
1 | CAT24C256WI-GT3OSCT-ND |  | U7
1 | M74VHC1GT14DFT2GOSCT-ND |  | U6
1 | Yost Lab 3 Space Sensor |  | U2
10 | 336-4490-1-ND |  | U5_FET1, U5_FET2, U5_FET3, U5_FET4, U5_FET5, U5_FET6, U5_FET7, U5_FET8, U5_FET9, U5_FET10
11 |  |  | J1_FET1, J1_FET2, J1_FET3, J1_FET4, J1_FET5, J1_FET6, J1_FET7, J1_FET8, J1_FET9, J1_FET10, J6
1 | 1276-3047-1-ND |  | C15
15 | 1276-1838-1-ND |  | C1, C3, C5, C7, C11, C13_FET1, C13_FET2, C13_FET3, C13_FET4, C13_FET5, C13_FET6, C13_FET7, C13_FET8, C13_FET9, C13_FET10
17 | 1276-6736-1-ND |  | C2, C4, C6, C8, C9, C10, C12, C14_FET1, C14_FET2, C14_FET3, C14_FET4, C14_FET5, C14_FET6, C14_FET7, C14_FET8, C14_FET9, C14_FET10
1 | 95278-101-46LF |  | P8
1 | 95278-101-46LF |  | P9
1 | MCP6284-E/SL-ND |  | U8
1 |  | DNP | CommsDisable
12 | WM14584-ND |  | 5V, FAN, SSR_FET1, SSR_FET2, SSR_FET3, SSR_FET4, SSR_FET5, SSR_FET6, SSR_FET7, SSR_FET8, SSR_FET9, SSR_FET10
3 | 900-2068320202-ND |  | PWR1, PWR2, Vbat
3 | WM10681-ND |  | BMS, RS485, TelemRadio
4 | WM7499-ND |  | A0, A1, A2, A3
1 | 445-2979-1-ND |  | L1
1 | SSM3K339RLFCT-ND |  | Q2
10 | 1727-8475-1-ND |  | Q1_FET1, Q1_FET2, Q1_FET3, Q1_FET4, Q1_FET5, Q1_FET6, Q1_FET7, Q1_FET8, Q1_FET9, Q1_FET10
1 | SSM3J338RLFCT-ND |  | Q3
1 | 311-150LRCT-ND |  | R38
1 | 311-200LRCT-ND |  | R35
14 | YAG3256CT-ND |  | R15, R16, R17, R18, R36_FET1, R36_FET2, R36_FET3, R36_FET4, R36_FET5, R36_FET6, R36_FET7, R36_FET8, R36_FET9, R36_FET10
2 | 311-0.0LRCT-ND |  | R8, R20
2 | RC0402FR-071K65L |  | R11, R37
23 | 311-60.4LRCT-ND |  | R1_FET1, R1_FET2, R1_FET3, R1_FET4, R1_FET5, R1_FET6, R1_FET7, R1_FET8, R1_FET9, R1_FET10, R9, R10, R22_FET1, R22_FET2, R22_FET3, R22_FET4, R22_FET5, R22_FET6, R22_FET7, R22_FET8, R22_FET9, R22_FET10, R25
3 | 311-2.49KLRCT-ND |  | R32, R33, R34
3 | YAG3043CT-ND |  | R12, R13, R14
5 | 311-4.7KLRCT-ND |  | R6, R19, R23, R24, R31
6 | 311-0.0LRCT-ND | DNP | R7, R21, R27, R28, R29, R30
25 | 36-5006-ND |  | TP1, TP2, TP3, TP4, TP5, TP6, TP7, TP8, TP9, TP10, TP11, TP12, TP13, TP14, TP15, TP16, TP17, TP18, TP19, TP23, TP24, TP25, TP26, TP27, TP28
10 | D12V0H1U2LP1610-7DIDKR-ND |  | D3_FET1, D3_FET2, D3_FET3, D3_FET4, D3_FET5, D3_FET6, D3_FET7, D3_FET8, D3_FET9, D3_FET10
10 | V2PM12HM3/HGICT-ND |  | D1_FET1, D1_FET2, D1_FET3, D1_FET4, D1_FET5, D1_FET6, D1_FET7, D1_FET8, D1_FET9, D1_FET10
3 | F10154CT-ND |  | D11, D17, D18
9 | 641-1764-1-ND |  | D9, D10, D12, D13, D14, D15, D16, D19, D20
14 | 732-11991-1-ND |  | D4_FET1, D4_FET2, D4_FET3, D4_FET4, D4_FET5, D4_FET6, D4_FET7, D4_FET8, D4_FET9, D4_FET10, D5, D6, D7, D8

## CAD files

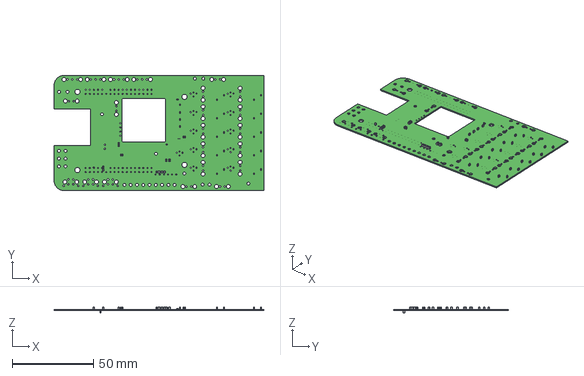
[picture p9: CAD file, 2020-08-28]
BeagleCape/Main.step
129.5 x 71.1 x 3.40 mm
Board
Extruded x 51

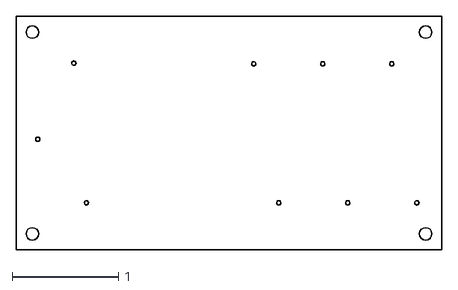
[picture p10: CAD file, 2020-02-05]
LegBoard/Schematics/Leg Board Top.dxf
4.00 x 2.20

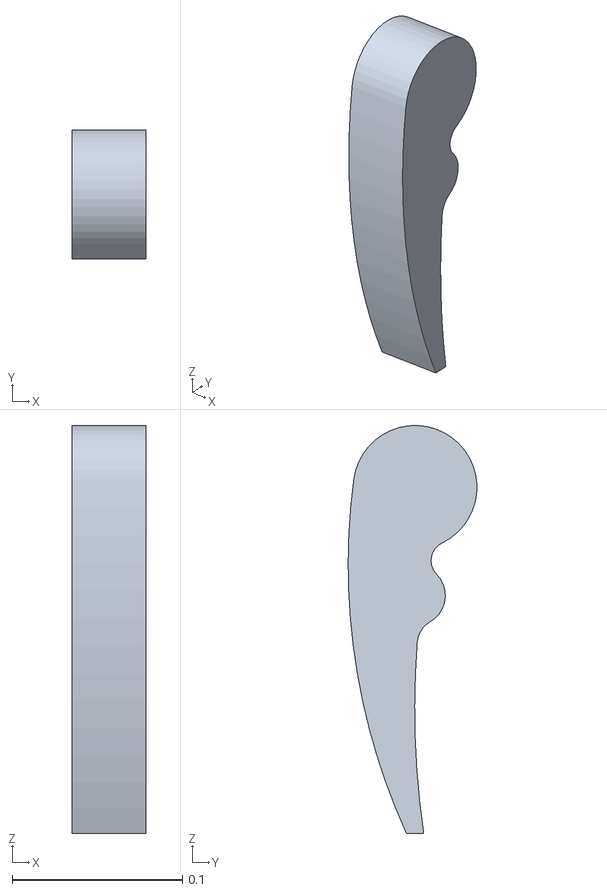
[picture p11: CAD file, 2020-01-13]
WalkingSimulation/Leg 1 Foot Simplified.obj
0.0432 x 0.0756 x 0.239

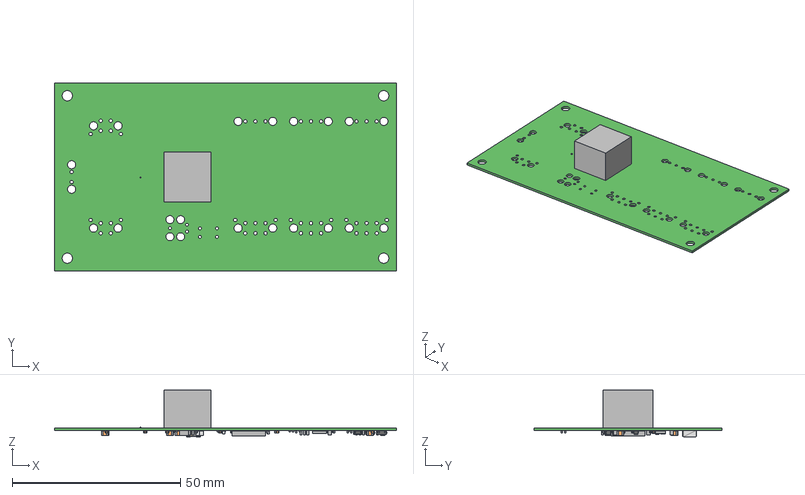
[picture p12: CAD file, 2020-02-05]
LegBoard/Schematics/LegBoard.step
101.6 x 55.9 x 13.8 mm
Board
CAPC1005X70N x 31
SOT95P237X111-3N x 2
Extruded x 23
RESC1005X40N x 9
MMBTH10LT3G--3DModel-STEP-56544 x 2
CAPC2012X145N x 8
INDC1608X100N x 2
IND_TAIYO_NRS4018

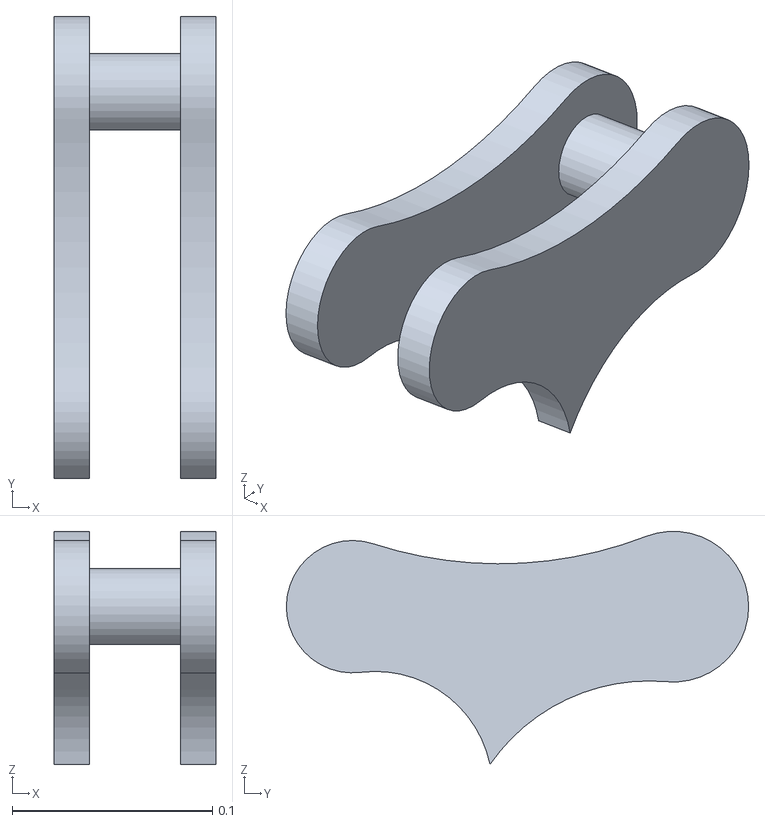
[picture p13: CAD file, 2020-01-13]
WalkingSimulation/Leg 1 Thigh Simplified.obj
0.0808 x 0.231 x 0.116

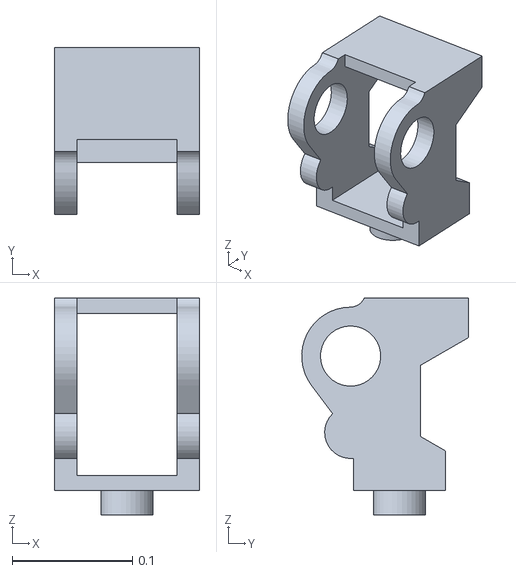
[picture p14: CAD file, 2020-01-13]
WalkingSimulation/Leg 1 Hip Simplified.obj
0.121 x 0.138 x 0.18

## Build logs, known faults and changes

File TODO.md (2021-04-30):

# BeagleBone

## System startup

  * Start telemetry on system boot

## Servo tuning while walking

  * leg_control listens on LEG_COMMAND for packets to send on modbus
  * Need to write tool to pack and send
  * Simultaneous on all legs
  * Enfield gain values (Gain, Damping, derivative, etc)

## Leg tool **#NextYear**

The feature set for a magical do-everything tool to configure the robot
firmware. For now, see Hull/Test/modbus_ui.c

  * Select leg by address
    * Scan for choices
  * Firmware update over modbus (as soon as the firmware supports it)!!!
  * Change address of selected leg
  * Display all feedback
    * Set polling frequency
    * Sensor Voltage
    * Angle
    * Length
    * Output voltage
    * Enfield command input
    * Rod pressure
    * Base pressure
    * adjust linearization parameters
      * min, max sensor voltage
      * min, max joint angle
      * min, max cylinder length
      * min, max output voltage
  * Tune servos
    * Set feedback polling frequency
    * All servo parameters (14 total)
    * All servo toggles (5 total)
    * Servo serial
    * Servo firmware rev
    * Plot command, feedback position
    * Manual position command
    * signal generator
      * set update period
      * sin/square
      * set signal period
      * set signal amplitude
      * set signal zero level
  * Command toe position

## Gait Generation
  * https://github.com/csiro-robotics/syropod_highlevel_controller
  * Optimization based gait
    * Find edges of leg working space? - Toe position -> joint angles -> joint
      angle limits.
    * At least three legs on the ground, not all on the same side of the robot
    * maintain specified velocity

## Telemetry
  * Radio works, `/dev/tty.mikrobus1`, 115200
  * Radio is RFD900x
  * Get telemetry branch merged!

## Pressure ADC
  * Uses internal ADC, depending on wiring read from
    /sys/bus/iio/devices/iio:device1/in_voltageN_raw
    to sample value.
  * read
    /sys/bus/iio/devices/iio:device1/in_voltage_scale
    for a scale to convert the raw value to voltage

## IMU
  * Pins enabled by [overlay](https://github.com/contradict/BeagleBoard-DeviceTrees/blob/v4.19.x-ti/src/arm/BBAI-SPI3-ADC-IMU.dts)
  * No signals verified with scope, no response from device. Sent message to
    Yost through website contact form, also no response.

## WiFi
  * hostapd configured /etc/hostapd.conf, SSID ChompTheBattlebot
  * interface configured /etc/network/interfaces wlan0 192.168.4.1/28
  * dnsmasq configured /etc/dnsmasq.conf DHCP range 192.168.4.2-14
  * DHCP requests arrive, responses sent (tcpdump)
  * Client never receives DHCP response (tcpdump)

# Leg Board

## Optimize kinematics
  * Complex results usually just use real part, don't compute complex part
  * Would DH parameters be better?

## Firmware update over modbus **#NextYear**

  * Firmare uses sectors 5, 6, 7, IVT in Sector 2
  * Bootloader in sector 4, IVT in Sector 1
  * Storage in Sector 3
  * On reset, bootloader check memory for special value, if not found sets
    VTOR for sector 2 and jumps to firmware reset

## Auto-addressing **#NextYear**
  * All boards boot with only all-call address (0x255)
  * Any board who's `UPSTREAM` input is high also responds to address 0x55
  * Modbus holding register write to change address (0x01)
  * Modbus coil write to set `DOWNSTREAM` output (0x01)
  * On boot, all `DOWNSTREAM` outputs are off.
  * To start addressing
      1. BeagleBone sets first `UPSTREAM`. GPIO needs to be wired on RS485
         Click.
      2. BeagleBone sets 0x55 board's address with write to 0x01
      3. BeagleBone de-asserts `UPSTREAM`
      4. BeagleBone asks newly addressed device to raise `DOWNSTREAM`
      5. BeagleBone sets 0x55 board's address with write to 0x01
      6. BeagleBone asks currently asserted device to de-assert
      7. repeat from 4 until all boards addressed

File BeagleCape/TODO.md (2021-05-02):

  * The fan connector was installed backwards, took it out and soldered a new one
in.

  * `5V` was not connected from our cape to the BeagleBone, I added a wire from
    `VDD_5V` (pins `P9.5` and `P9.6`) to the cape `5V` rail.

  * The `COMMUP/DOWN` line from the leg boards was connected to `P9.09`, which
    turns out to be the power button. I disconnected that for now, this should
    be moved to a different pin.

  * Resistors:  If possible, no resistor smaller than 0603, any user installable
     jump resistor should be at least 0804, preferably 1206 if possible.

  * PWM?:  Put as many of the FET control inputs on header pins that can be
      connected to the PRU IO pins.  This might allow us to do clever peak
      and hold schemes with the big solenoids, or use the battery to run the
      ignitors with a 50% duty cycle.

  * Check all LED direction to make sure they are installed correctly (per Russel in slack on 10/31/20 the high current outputs appear to be soldered on backwards).

  * S.port interface cannot work. TXD idles high, so as long as the pin is
    connected to the UART, Q2 holds the line low. I think Q2 and associated
    components need to be replaced with a tri-state driver with the enable line
    connected to uart8_rtsn - P8.32. P8.32 is currently used for a high
    current output so that will need to be reassigned too.

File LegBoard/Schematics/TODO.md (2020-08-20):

* The rest of Chomp has pin 1 always ground. We should switch to this convention
* The 6-pin connector symbol and footprint have different pinouts. The footprint
    is correct.
* The Debug connector is difficult to install. It should be rotated 90 degrees
    or moved at least 0.5" from any tall components.
* Spread out the LEDs so each one is in line with the servo connectors it
    represents
* Add one more LED near the Communication connectors
* Add non-volatile storage. A >2kbit I2C EEPROM would be a good choice. It would
    also be interesting to explore the battery-backed SRAM on chip, maybe just a
    small lithium battery could solve this.
* I would like to have some testpoints
    * 4 microprocessor pins brought to plated holes
    * 6 LED controller pins brought to plated holes
* Power control of the Enfields would be very nice, individual would be best,
  but if it had to be all of them at once I could work with that.

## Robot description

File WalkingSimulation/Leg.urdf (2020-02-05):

<?xml version="1.0"?>
<!-- vim: set ft=xml sw=2 : -->
<robot name="Stomp">
  <link name="base">
    <visual>
      <geometry>
        <box size="0.3 0.3 0.02"/>
      </geometry>
      <origin xyz="0 0 -0.01"/>
    </visual>
  </link>
  <joint name="pivot" type="continuous">
    <parent link="base"/>
    <child link="hip"/>
    <axis xyz="0 0 1"/>
    <origin xyz="0.0 -0.11 0.11" rpy="0 0 0"/>
  </joint>
  <link name="hip">
    <visual>
      <geometry>
        <mesh filename="Leg 1 Hip Simplified.obj"/>
      </geometry>
    </visual>
    <inertial>
      <origin xyz="-0.002 -0.004 -0.025"/>
      <mass value="2.067"/>
      <inertia ixx="0.009" ixy="0" ixz="0" iyy="0.011" iyz="-0.001" izz="0.007"/>
    </inertial>
    <collision>
    </collision>
  </link>
  <!--
  <joint name="pivot_cylinder_base" type="continuous">
    <parent link="base"/>
    <child link="pivot_cylinder"/>
    <origin xyz="-0.06543 0.0915 0.135" rpy="0 1.57 0"/>
    <axis xyz="0 0 1"/>
  </joint>
  <link name="pivot_cylinder">
    <visual>
      <geometry>
        <cylinder length="0.10" radius="0.027"/>
      </geometry>
      <origin xyz="0 0 -0.05"/>
    </visual>
  </link>
  <joint name="pivot_cylinder_slide" type="prismatic">
    <parent link="pivot_cylinder"/>
    <child link="pivot_rod"/>
    <axis xyz="0 0 1"/>
  </joint>
  <link name="pivot_rod">
    <visual>
      <geometry>
        <cylinder length="0.10" radius="0.01"/>
      </geometry>
    </visual>
  </link>
  <joint name="pivot_yoke" type="continuous">
    <parent link="pivot_rod"/>
    <child link="hip"/>
    <origin xyz="0 0.099 0"/>
  </joint>
  -->
  <joint name="knee" type="continuous">
    <parent link="hip" />
    <child link="thigh" />
    <origin xyz="0 -0.041 0.0" />
    <axis xyz="1 0 0" />
  </joint>
  <link name="thigh">
    <visual>
      <geometry>
        <mesh filename="Leg 1 Thigh Simplified.obj"/>
      </geometry>
    </visual>
    <inertial>
      <origin xyz="0 -0.048 -0.003"/>
      <mass value="1.512"/>
      <inertia ixx="0.01" ixy="0" ixz="0" iyy="0.002" iyz="0" izz="0.011"/>
    </inertial>
    <collision>
    </collision>
  </link>
  <joint name="ankle" type="continuous">
    <parent link="thigh" />
    <child link="foot" />
    <origin xyz="0 -0.160 0" />
    <axis xyz="1 0 0" />
  </joint>
  <link name="foot">
    <visual>
      <geometry>
        <mesh filename="Leg 1 Foot Simplified.obj"/>
      </geometry>
    </visual>
    <inertial>
      <origin xyz="0 -0.008 -0.053"/>
      <mass value="0.600"/>
      <inertia ixx=".003" ixy="0" ixz="0" iyy="0.002" iyz="0" izz="0.0003"/>
    </inertial>
  </link>
</robot>

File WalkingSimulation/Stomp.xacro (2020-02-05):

<?xml version="1.0"?>
<!-- vim: set ft=xml sw=2 : -->
<robot xmlns:xacro="http://www.ros.org/wiki/xacro" name="Stomp">
  <xacro:macro name="leg" params="idx parent position orientation">
    <joint name="leg_pivot_${idx}" type="continuous">
      <parent link="${parent}"/>
      <child link="leg_hip_${idx}"/>
      <axis xyz="0 0 1"/>
      <origin xyz="${position}" rpy="${orientation}"/>
    </joint>
    <link name="leg_hip_${idx}">
      <visual>
        <geometry>
          <mesh filename="Leg 1 Hip Simplified.obj"/>
        </geometry>
      </visual>
      <inertial>
        <origin xyz="-0.002 -0.004 -0.025"/>
        <mass value="2.067"/>
        <inertia ixx="0.009" ixy="0" ixz="0" iyy="0.011" iyz="-0.001" izz="0.007"/>
      </inertial>
      <collision>
        <geometry>
          <mesh filename="Leg 1 Hip Simplified.obj"/>
        </geometry>
      </collision>
    </link>
    <!--
    <joint name="leg_pivot_cylinder_base_${idx}" type="continuous">
      <parent link="base"/>
      <child link="leg_pivot_cylinder_${idx}"/>
      <origin xyz="-0.06543 0.0915 0.135" rpy="0 1.57 0"/>
      <axis xyz="0 0 1"/>
    </joint>
    <link name="leg_pivot_cylinder_${idx}">
      <visual>
        <geometry>
          <cylinder length="0.10" radius="0.027"/>
        </geometry>
        <origin xyz="0 0 -0.05"/>
      </visual>
    </link>
    <joint name="leg_pivot_cylinder_slide_${idx}" type="prismatic">
      <parent link="leg_pivot_cylinder_${idx}"/>
      <child link="leg_pivot_rod_${idx}"/>
      <axis xyz="0 0 1"/>
    </joint>
    <link name="leg_pivot_rod_${idx}">
      <visual>
        <geometry>
          <cylinder length="0.10" radius="0.01"/>
        </geometry>
      </visual>
    </link>
    <joint name="leg_pivot_yoke_${idx}" type="continuous">
      <parent link="leg_pivot_rod_${idx}"/>
      <child link="hip"/>
      <origin xyz="0 0.099 0"/>
    </joint>
    -->
    <joint name="leg_knee_${idx}" type="continuous">
      <parent link="leg_hip_${idx}" />
      <child link="leg_thigh_${idx}" />
      <origin xyz="0 -0.041 0.0" />
      <axis xyz="1 0 0" />
    </joint>
    <link name="leg_thigh_${idx}">
      <visual>
        <geometry>
          <mesh filename="Leg 1 Thigh Simplified.obj"/>
        </geometry>
      </visual>
      <inertial>
        <origin xyz="0 -0.048 -0.003"/>
        <mass value="1.512"/>
        <inertia ixx="0.01" ixy="0" ixz="0" iyy="0.002" iyz="0" izz="0.011"/>
      </inertial>
      <collision>
        <geometry>
          <mesh filename="Leg 1 Thigh Simplified.obj"/>
        </geometry>
      </collision>
    </link>
    <joint name="leg_ankle_${idx}" type="continuous">
      <parent link="leg_thigh_${idx}" />
      <child link="leg_foot_${idx}" />
      <origin xyz="0 -0.160 0" />
      <axis xyz="1 0 0" />
    </joint>
    <link name="leg_foot_${idx}">
      <visual>
        <geometry>
          <mesh filename="Leg 1 Foot Simplified.obj"/>
        </geometry>
      </visual>
      <inertial>
        <origin xyz="0 -0.008 -0.053"/>
        <mass value="0.600"/>
        <inertia ixx=".003" ixy="0" ixz="0" iyy="0.002" iyz="0" izz="0.0003"/>
      </inertial>
      <collision>
        <geometry>
          <mesh filename="Leg 1 Foot Simplified.obj"/>
        </geometry>
      </collision>
    </link>
  </xacro:macro>
  <link name="base">
    <visual>
      <geometry>
        <box size="0.72 0.3 0.02"/>
      </geometry>
      <origin xyz="0 0 -0.01"/>
    </visual>
  </link>
  <xacro:leg idx="0" parent="base" position=" 0.30 -0.11 0.112" orientation="0 0 0"/>
  <xacro:leg idx="1" parent="base" position=" 0.00 -0.11 0.112" orientation="0 0 0"/>
  <xacro:leg idx="2" parent="base" position="-0.30 -0.11 0.112" orientation="0 0 0"/>
  <xacro:leg idx="3" parent="base" position="-0.30 0.11 0.112" orientation="0 0 ${pi}"/>
  <xacro:leg idx="4" parent="base" position=" 0.00 0.11 0.112" orientation="0 0 ${pi}"/>
  <xacro:leg idx="5" parent="base" position=" 0.30 0.11 0.112" orientation="0 0 ${pi}"/>
</robot>

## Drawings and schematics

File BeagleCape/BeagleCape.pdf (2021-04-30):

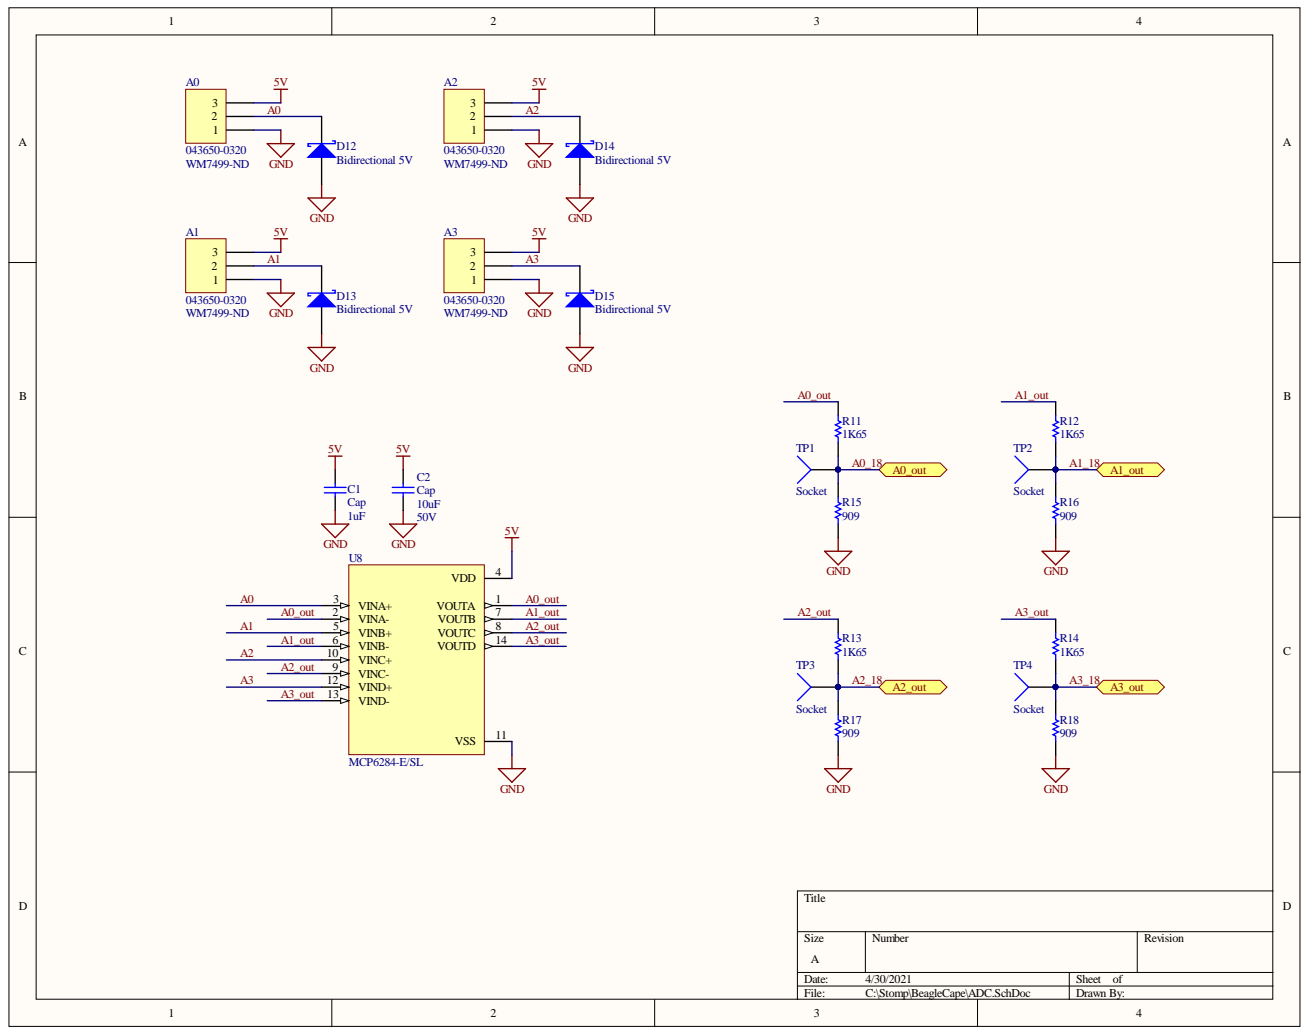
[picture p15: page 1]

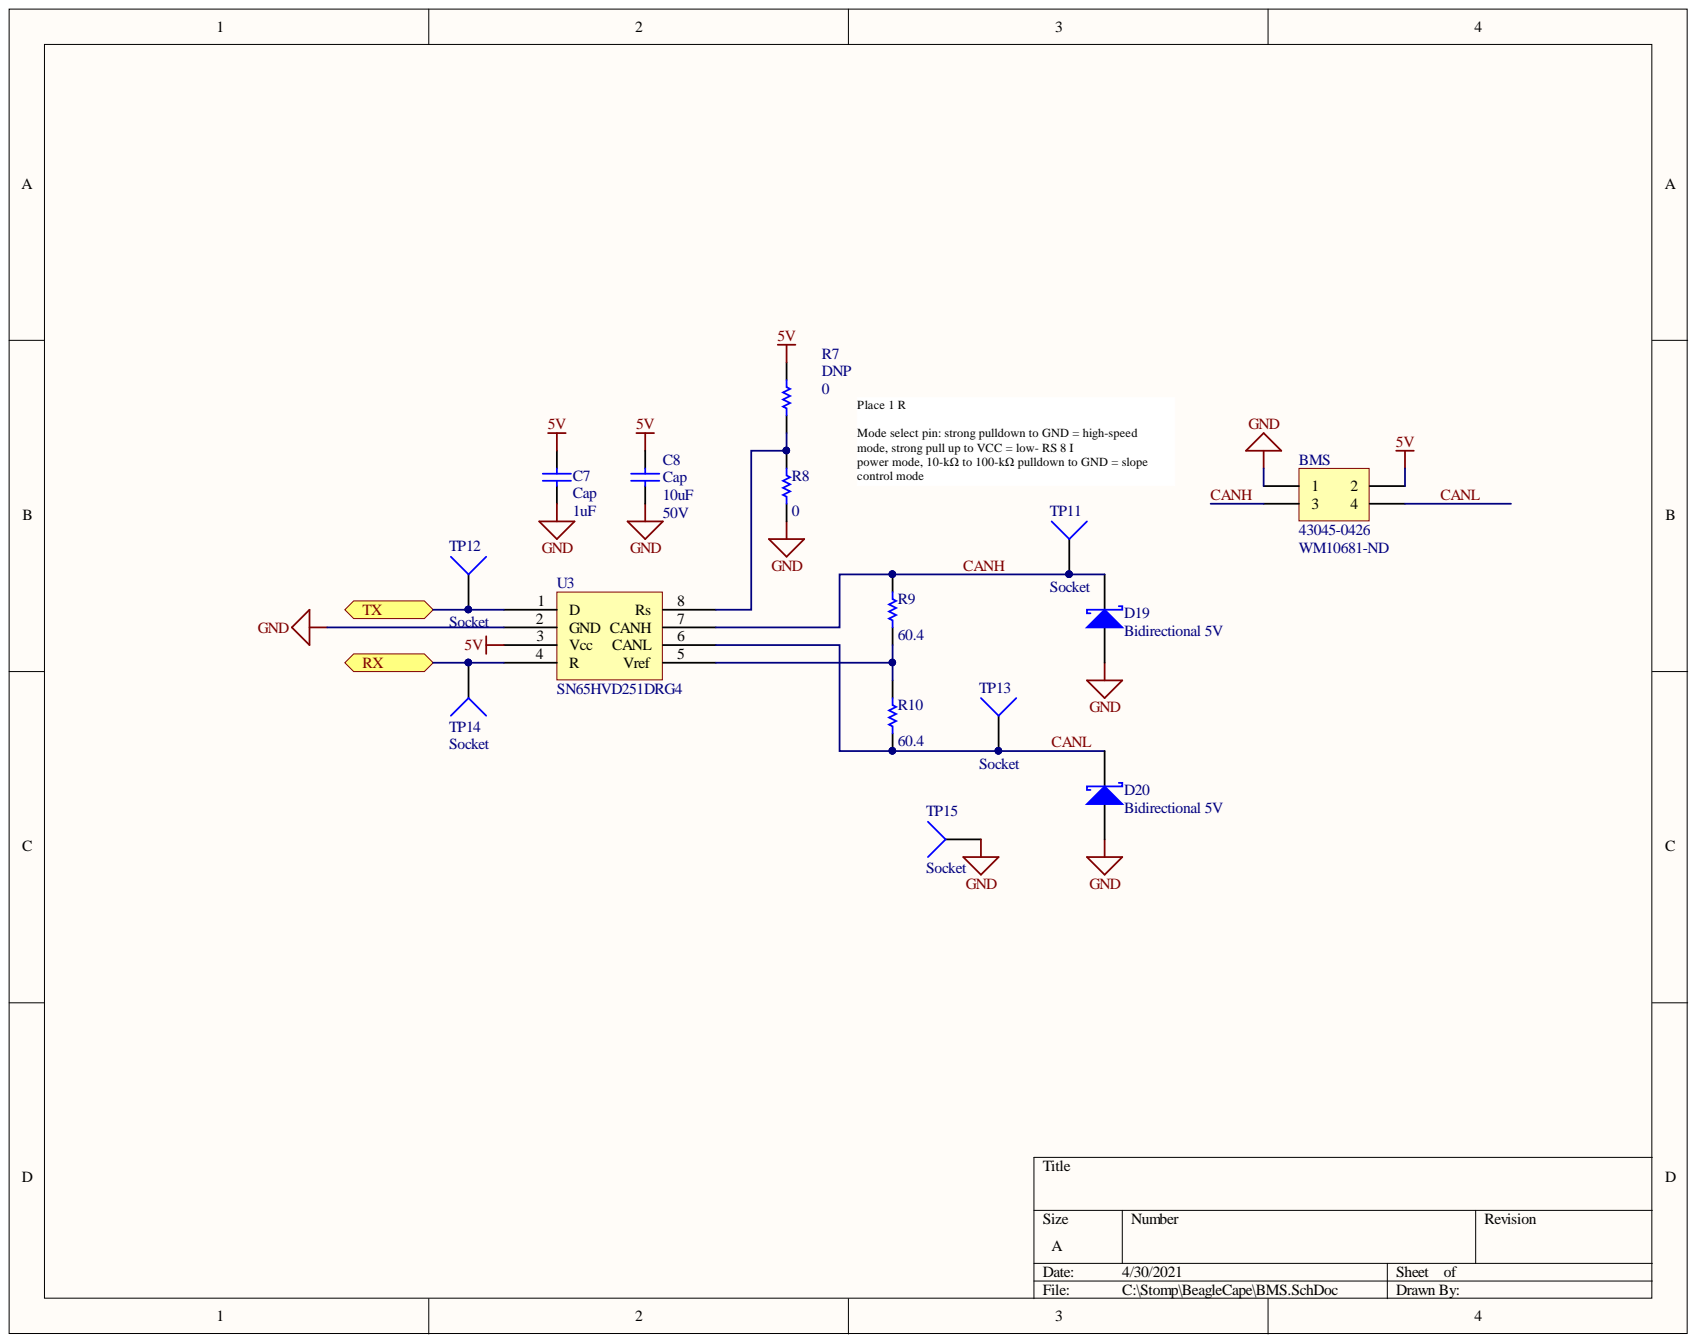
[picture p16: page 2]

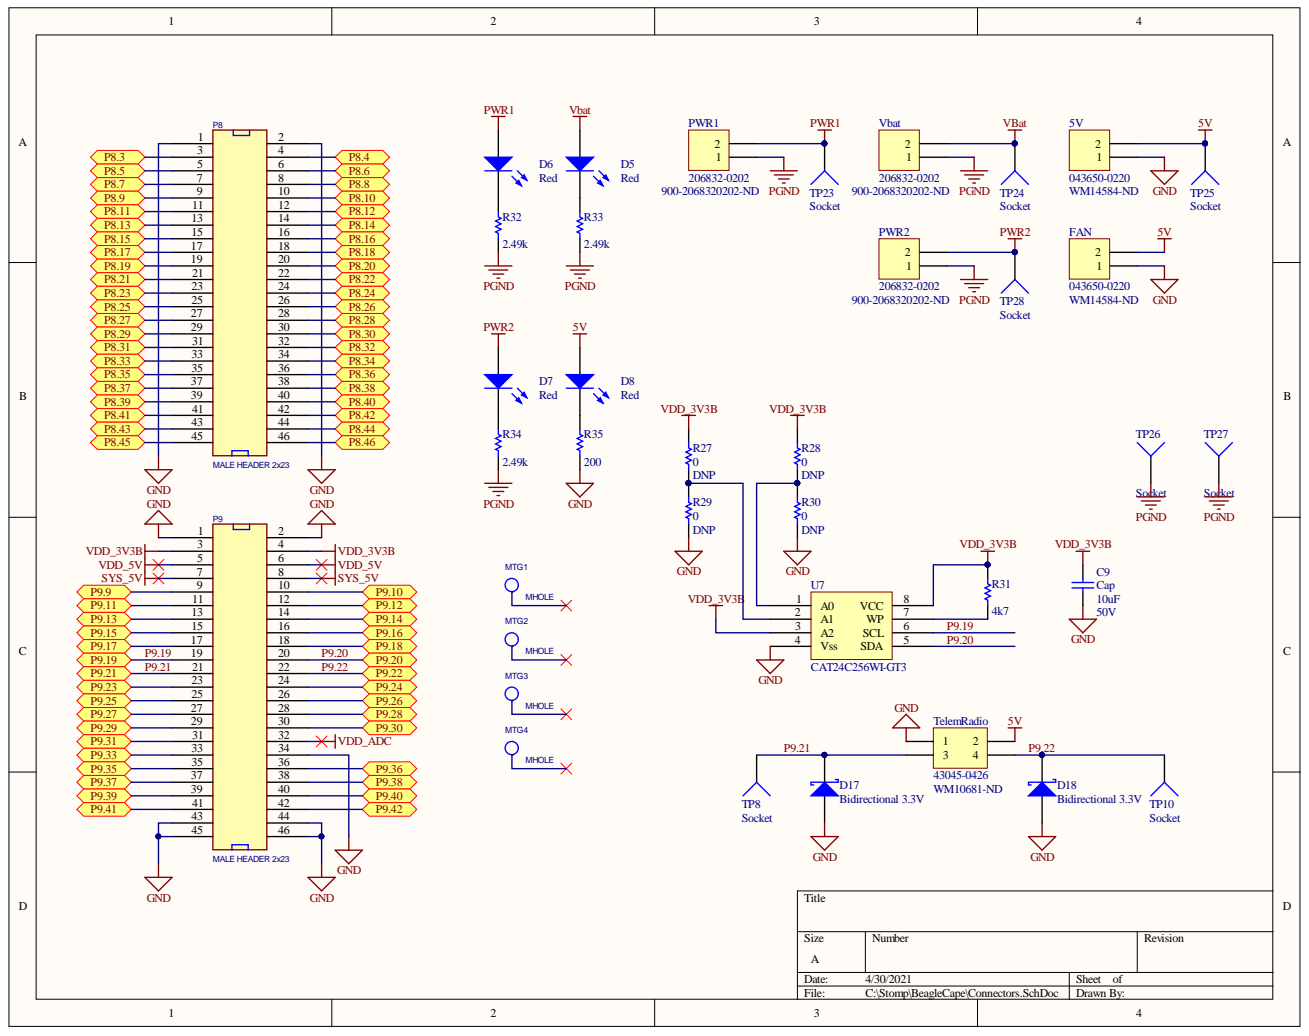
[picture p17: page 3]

1 1 | 1 2
1 3 | 1 4
1 5 | 1 6

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
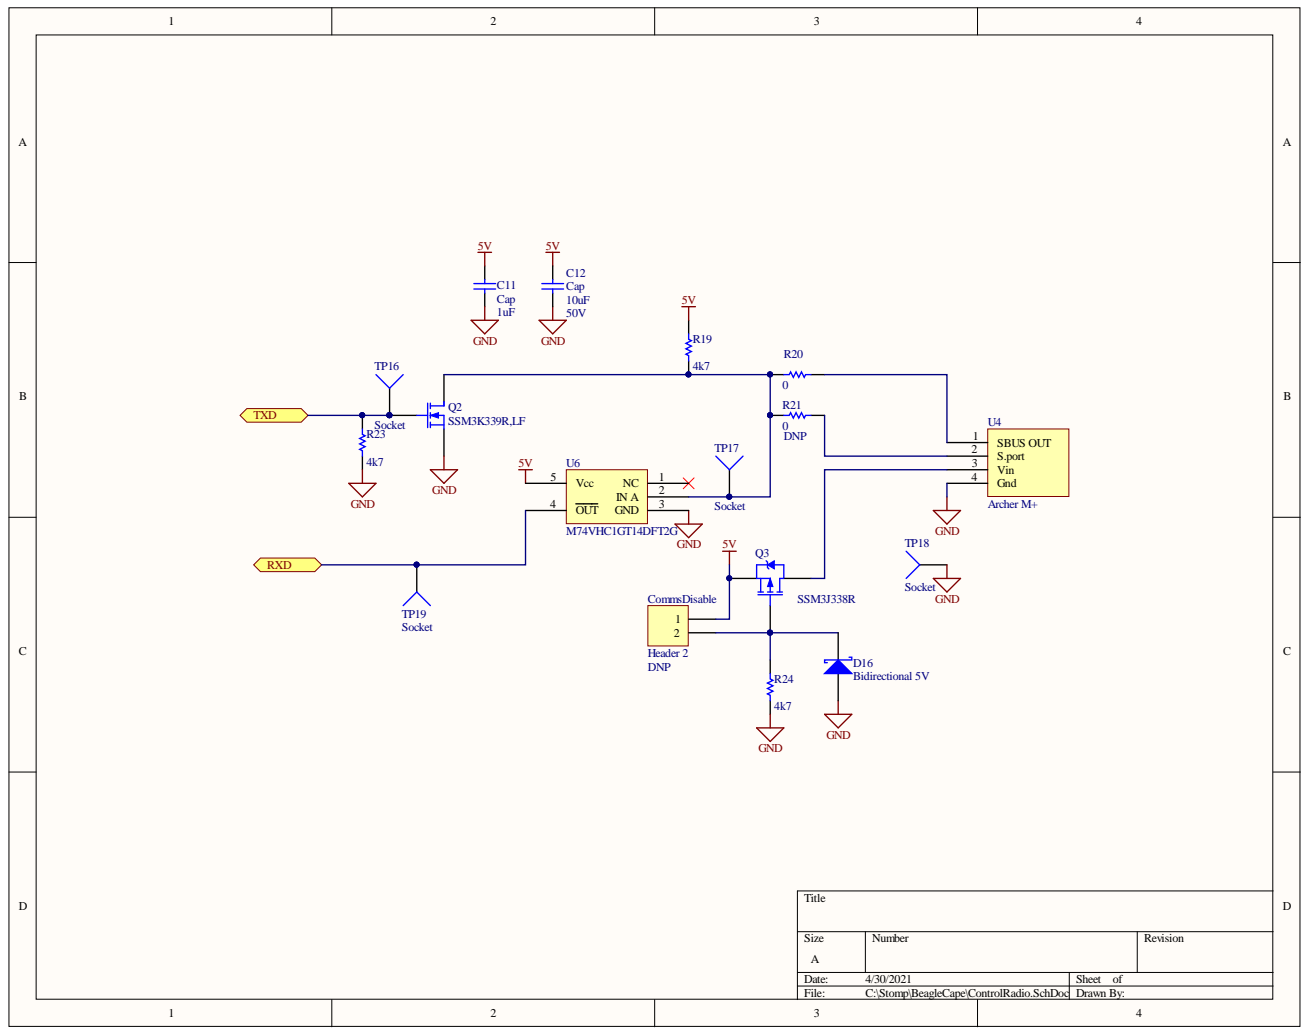
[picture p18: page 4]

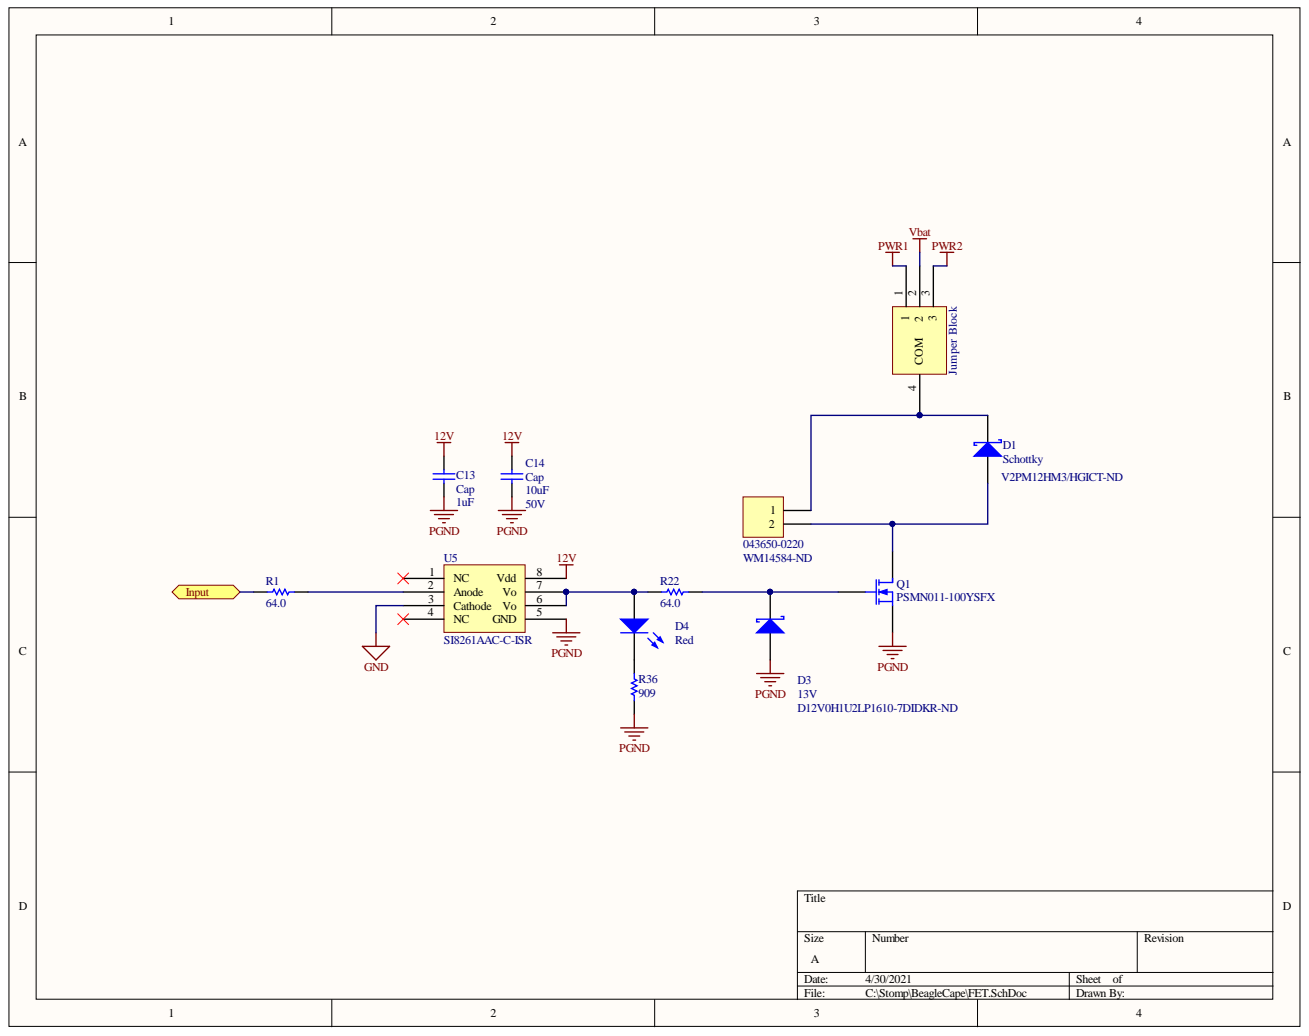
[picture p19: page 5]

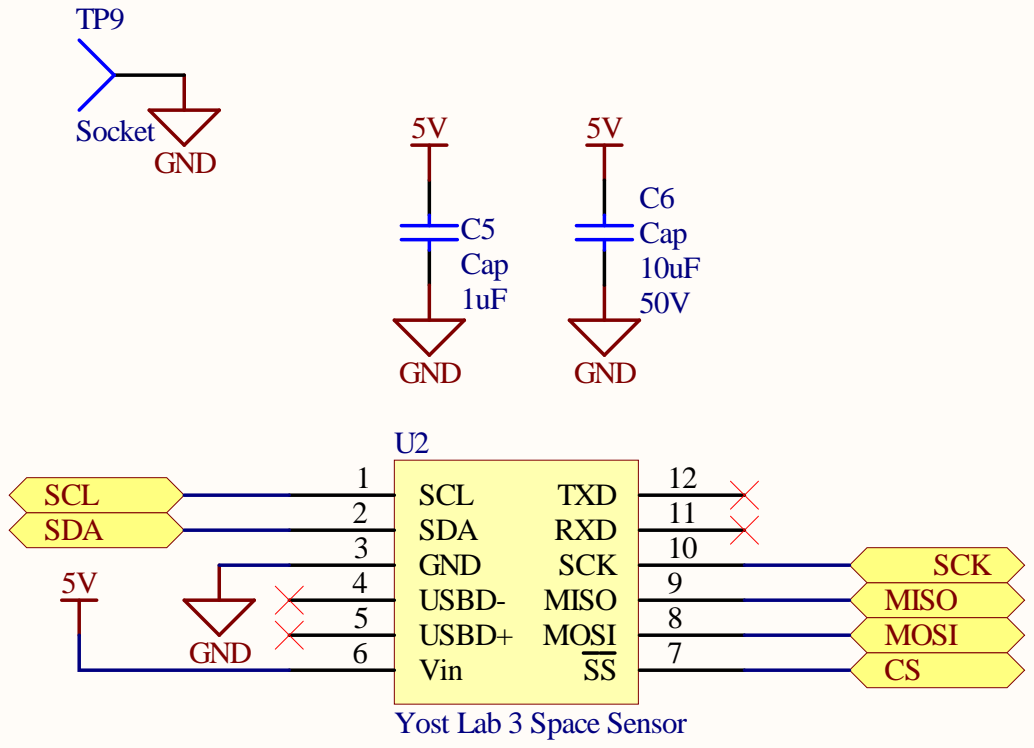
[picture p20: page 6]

Yost Lab 3 Space Sensor

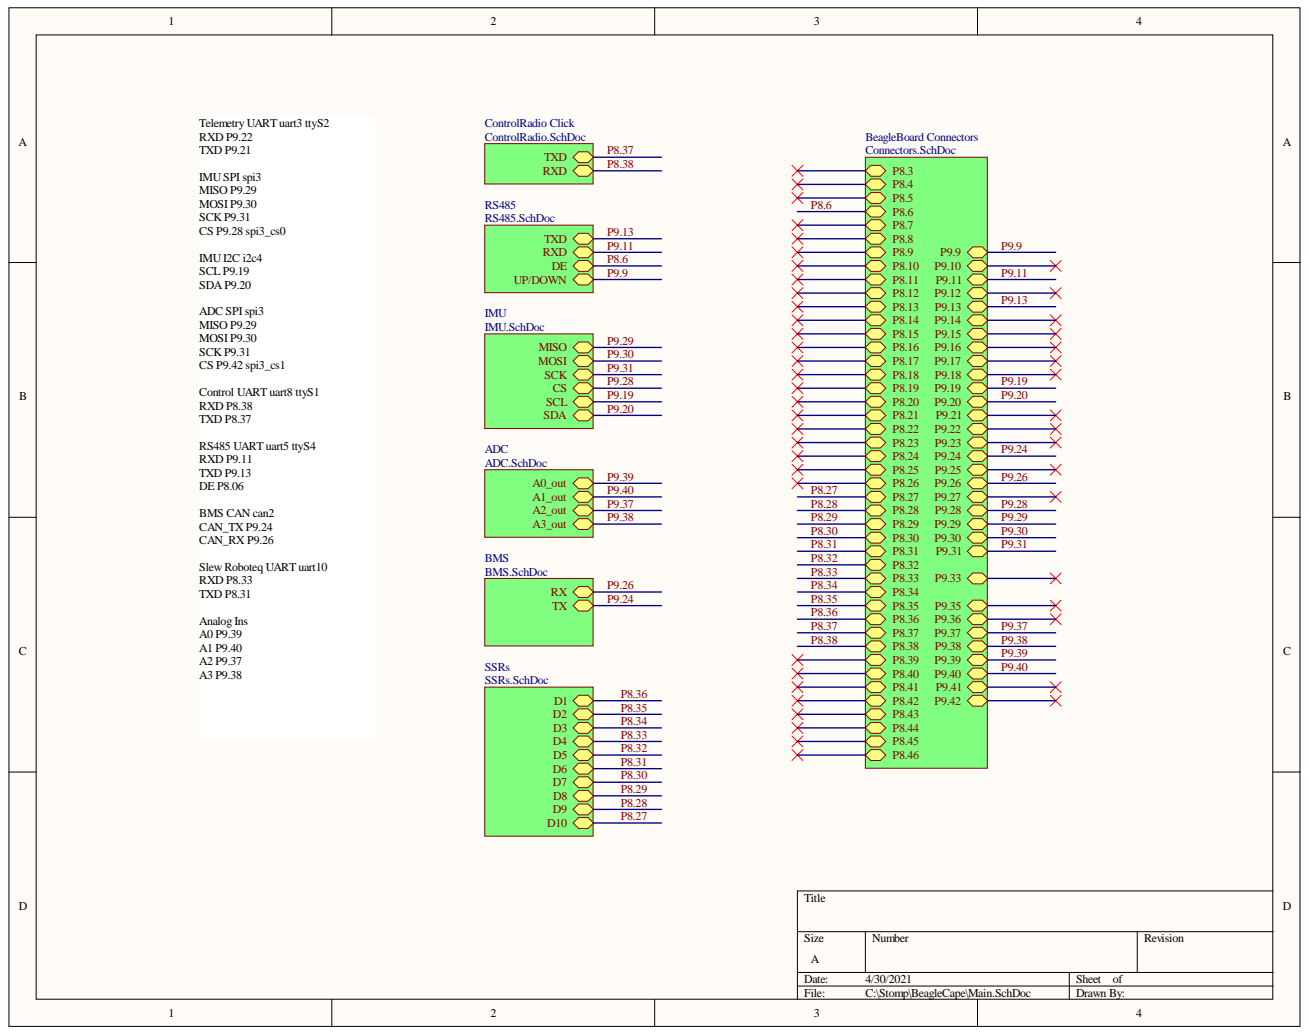
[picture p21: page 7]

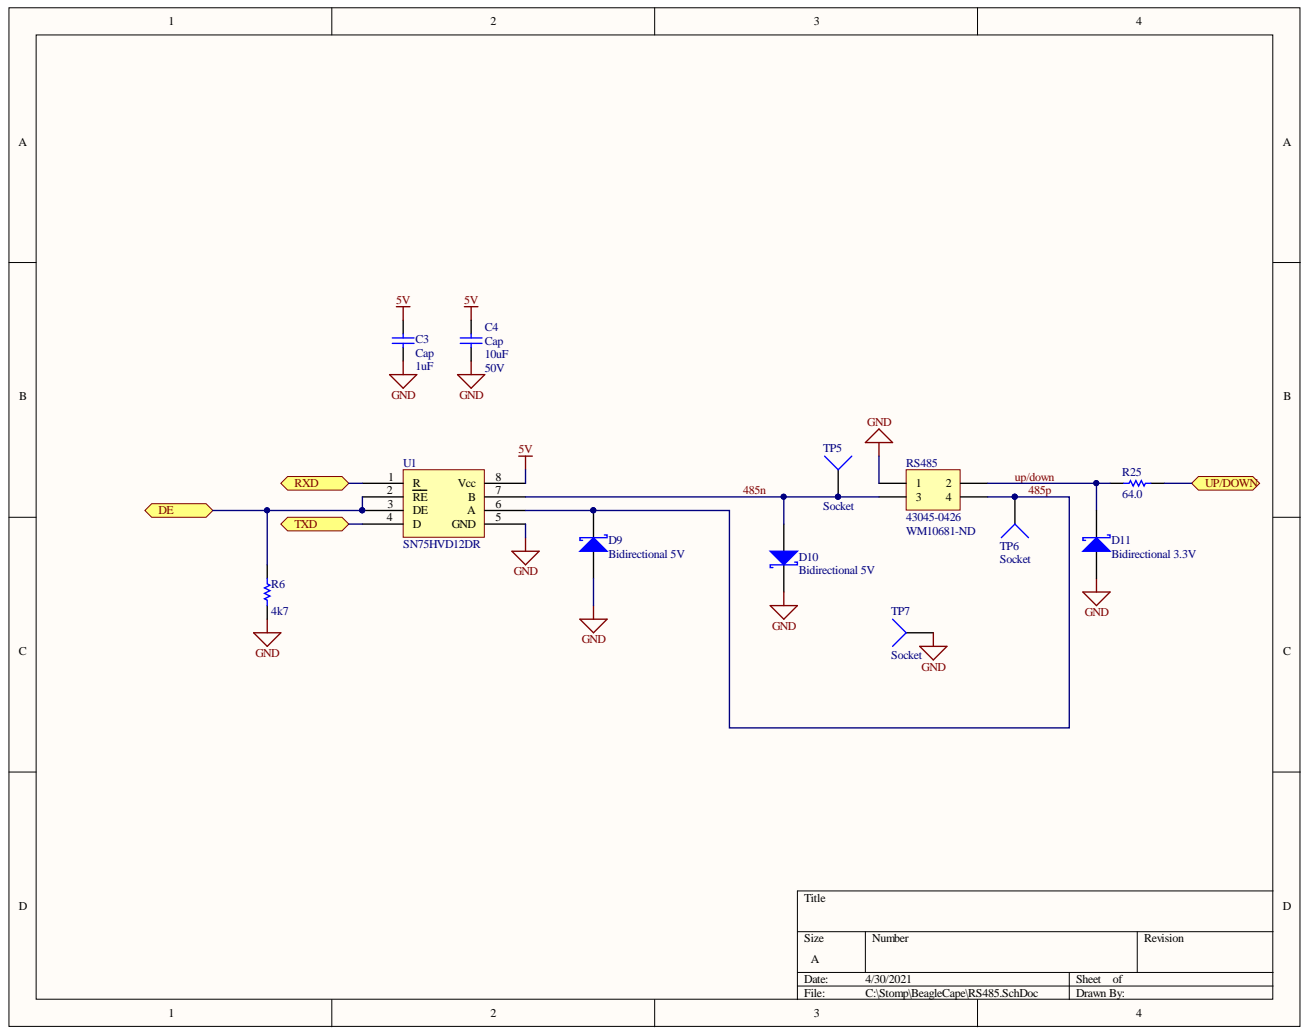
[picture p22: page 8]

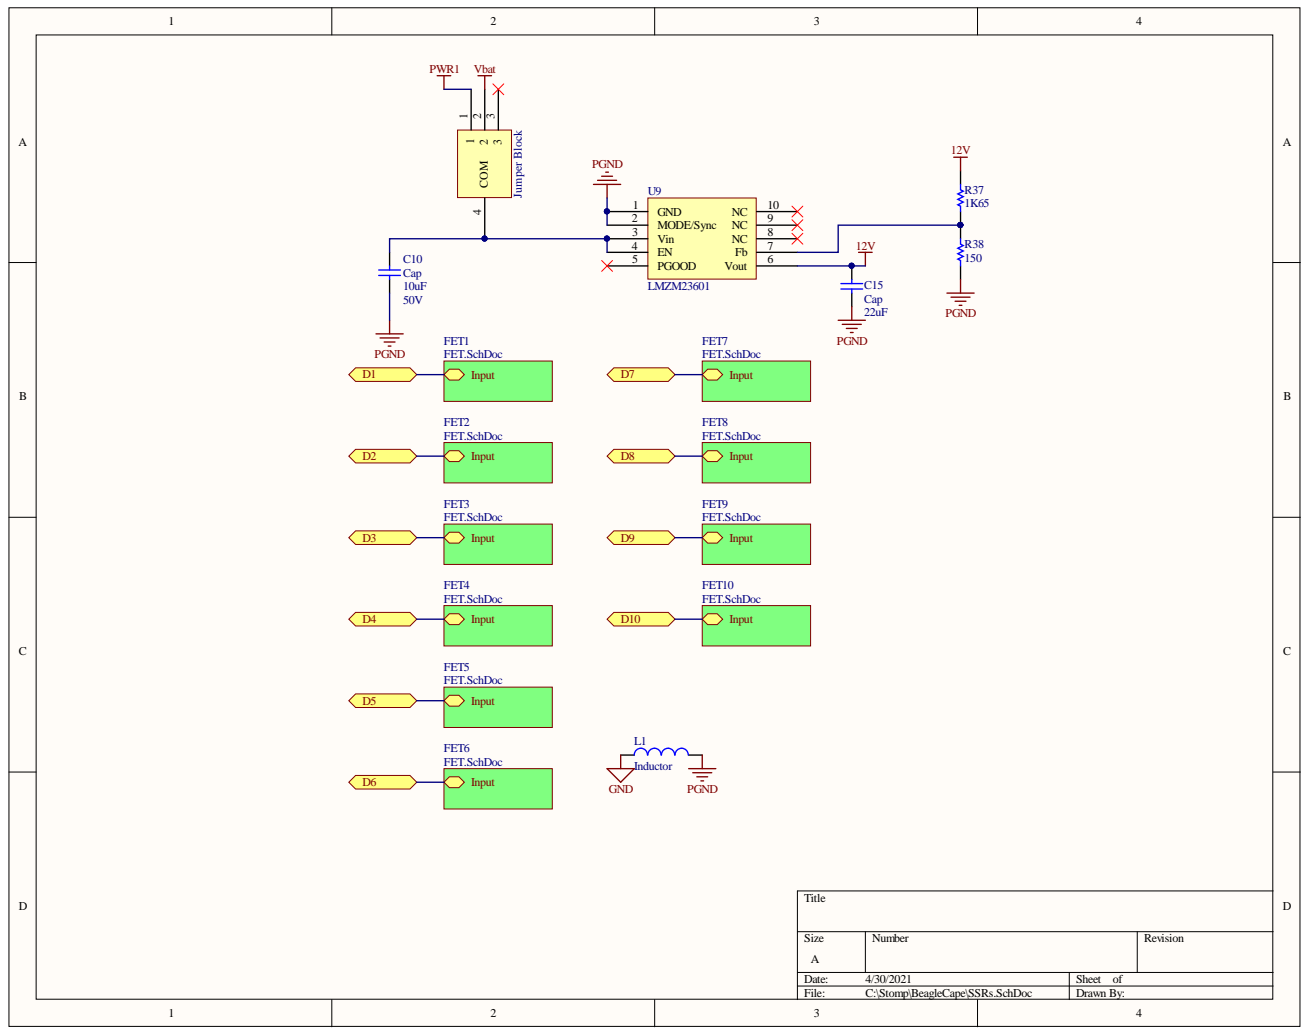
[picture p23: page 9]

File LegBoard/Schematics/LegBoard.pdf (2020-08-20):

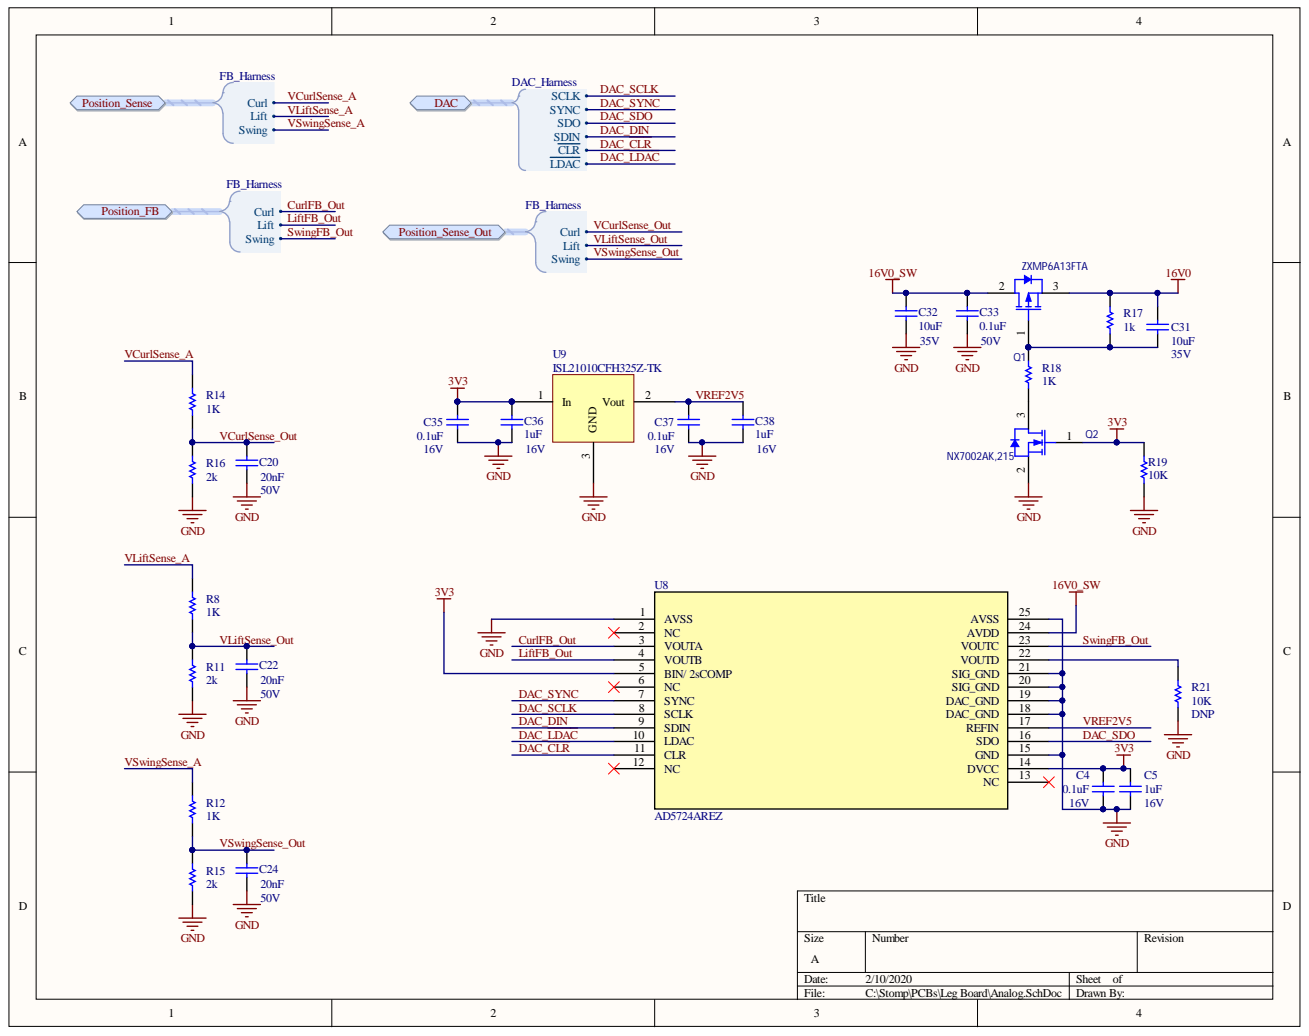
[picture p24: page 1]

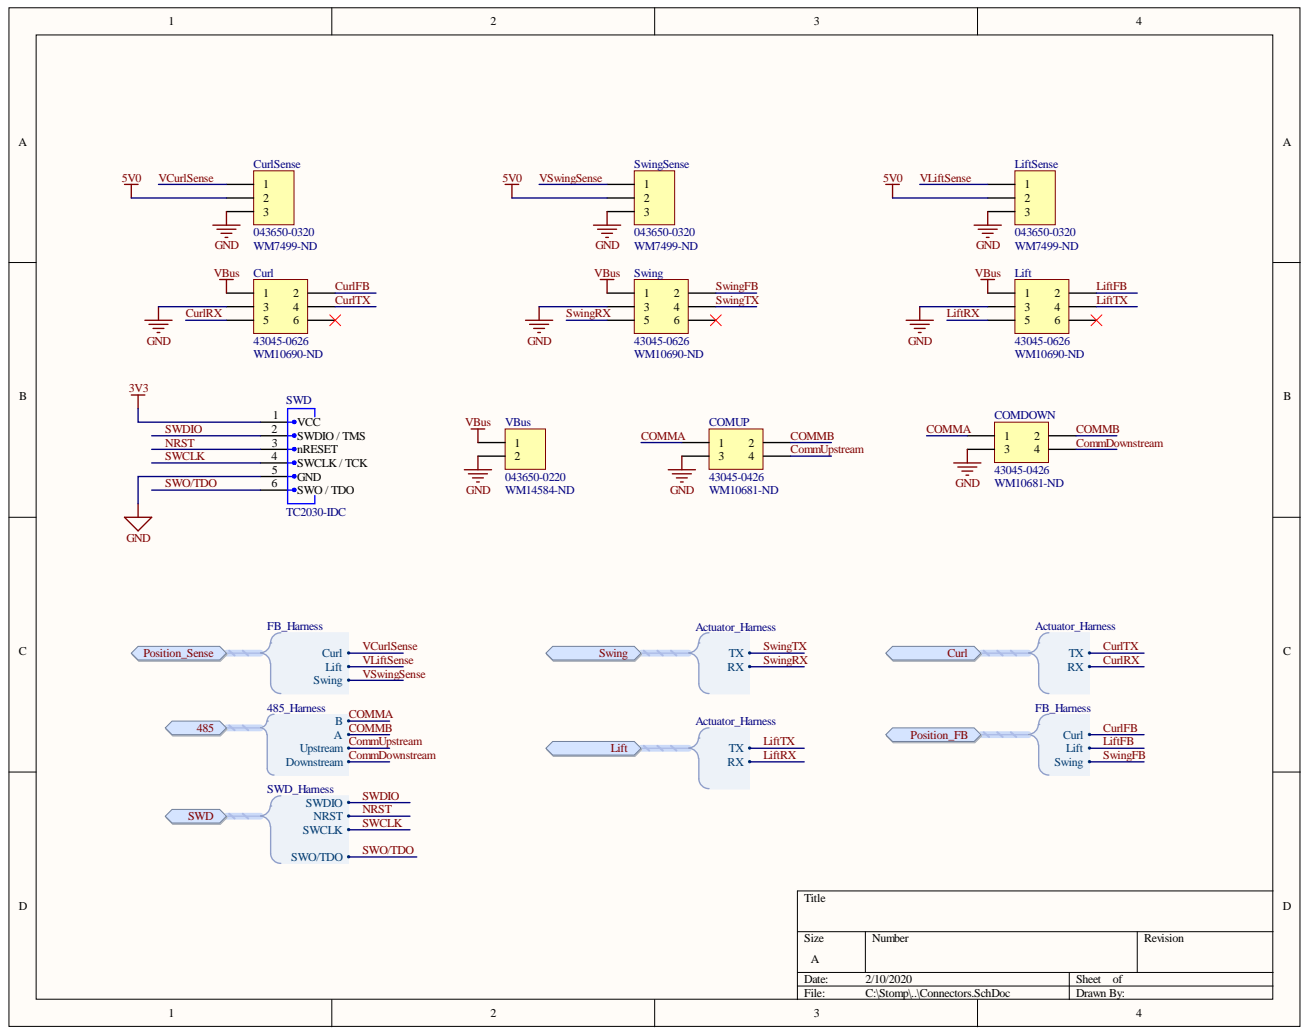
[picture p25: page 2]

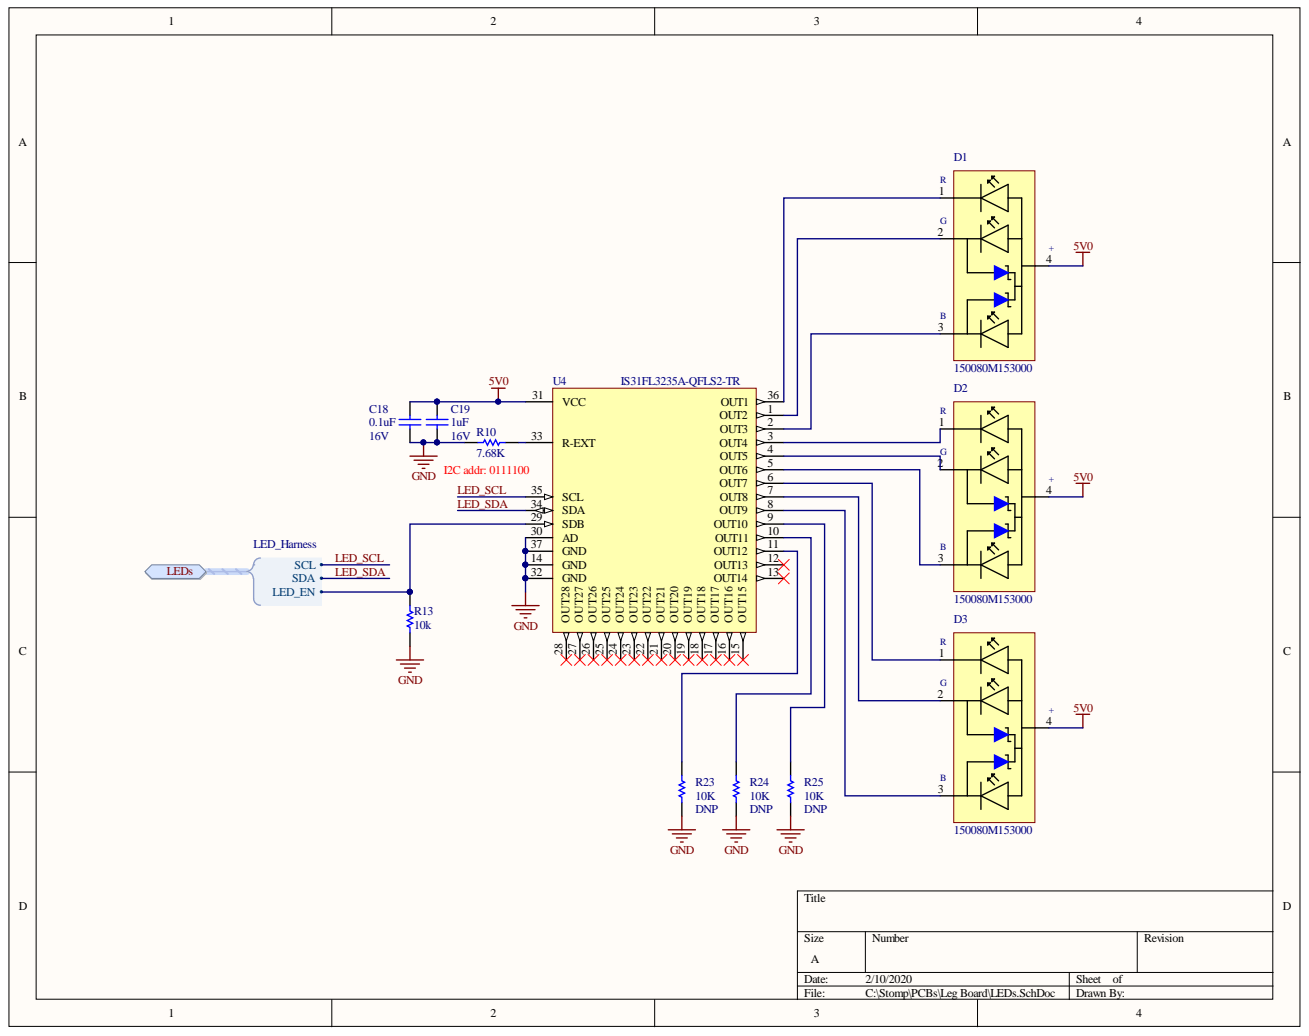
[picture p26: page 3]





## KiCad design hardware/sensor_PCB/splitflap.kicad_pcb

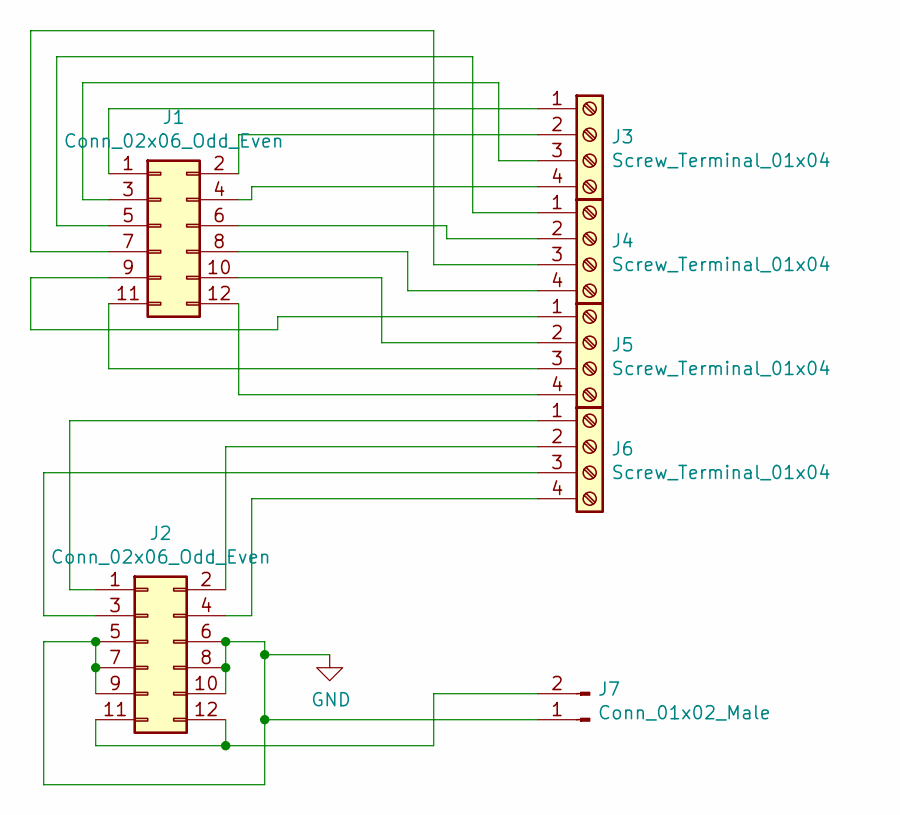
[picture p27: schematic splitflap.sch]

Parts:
J1, J2: Conn_02x06_Odd_Even; IDC-Header_2x06_P2.54mm_Vertical
J3, J4, J5, J6: Screw_Terminal_01x04; TerminalBlock_bornier-4_P5.08mm
J7: Conn_01x02_Male; JST_EH_B2B-EH-A_1x02_P2.50mm_Vertical

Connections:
GND: J2.5, J2.6, J2.7, J2.8, J2.9, J2.10, J7.1
unnamed: J1.1, J3.1
unnamed: J1.2, J3.2
unnamed: J1.3, J3.3
unnamed: J1.4, J3.4
unnamed: J1.5, J4.1
unnamed: J1.6, J4.2
unnamed: J1.7, J4.3
unnamed: J1.8, J4.4
unnamed: J1.9, J5.1
unnamed: J1.10, J5.2
unnamed: J1.11, J5.3
unnamed: J1.12, J5.4
unnamed: J2.1, J6.1
unnamed: J2.2, J6.2
unnamed: J2.3, J6.3
unnamed: J2.4, J6.4
unnamed: J2.11, J2.12, J7.2

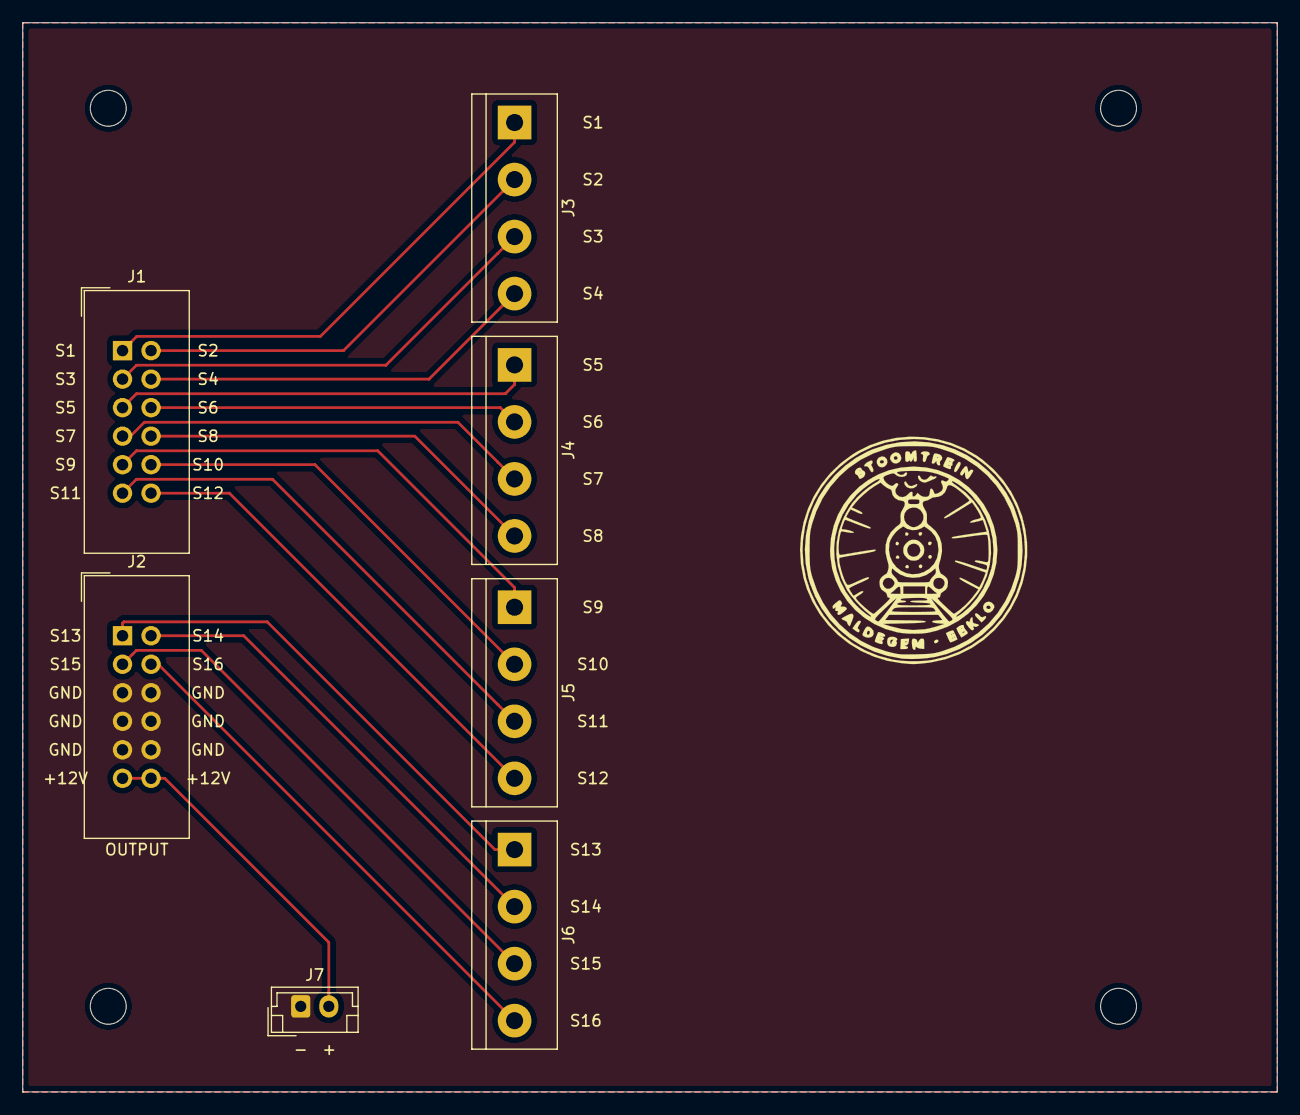
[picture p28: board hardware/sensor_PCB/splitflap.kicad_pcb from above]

Board: 2 copper layers, 111.8 x 95.2 mm, 7 parts (0 on the bottom side), 18 nets.

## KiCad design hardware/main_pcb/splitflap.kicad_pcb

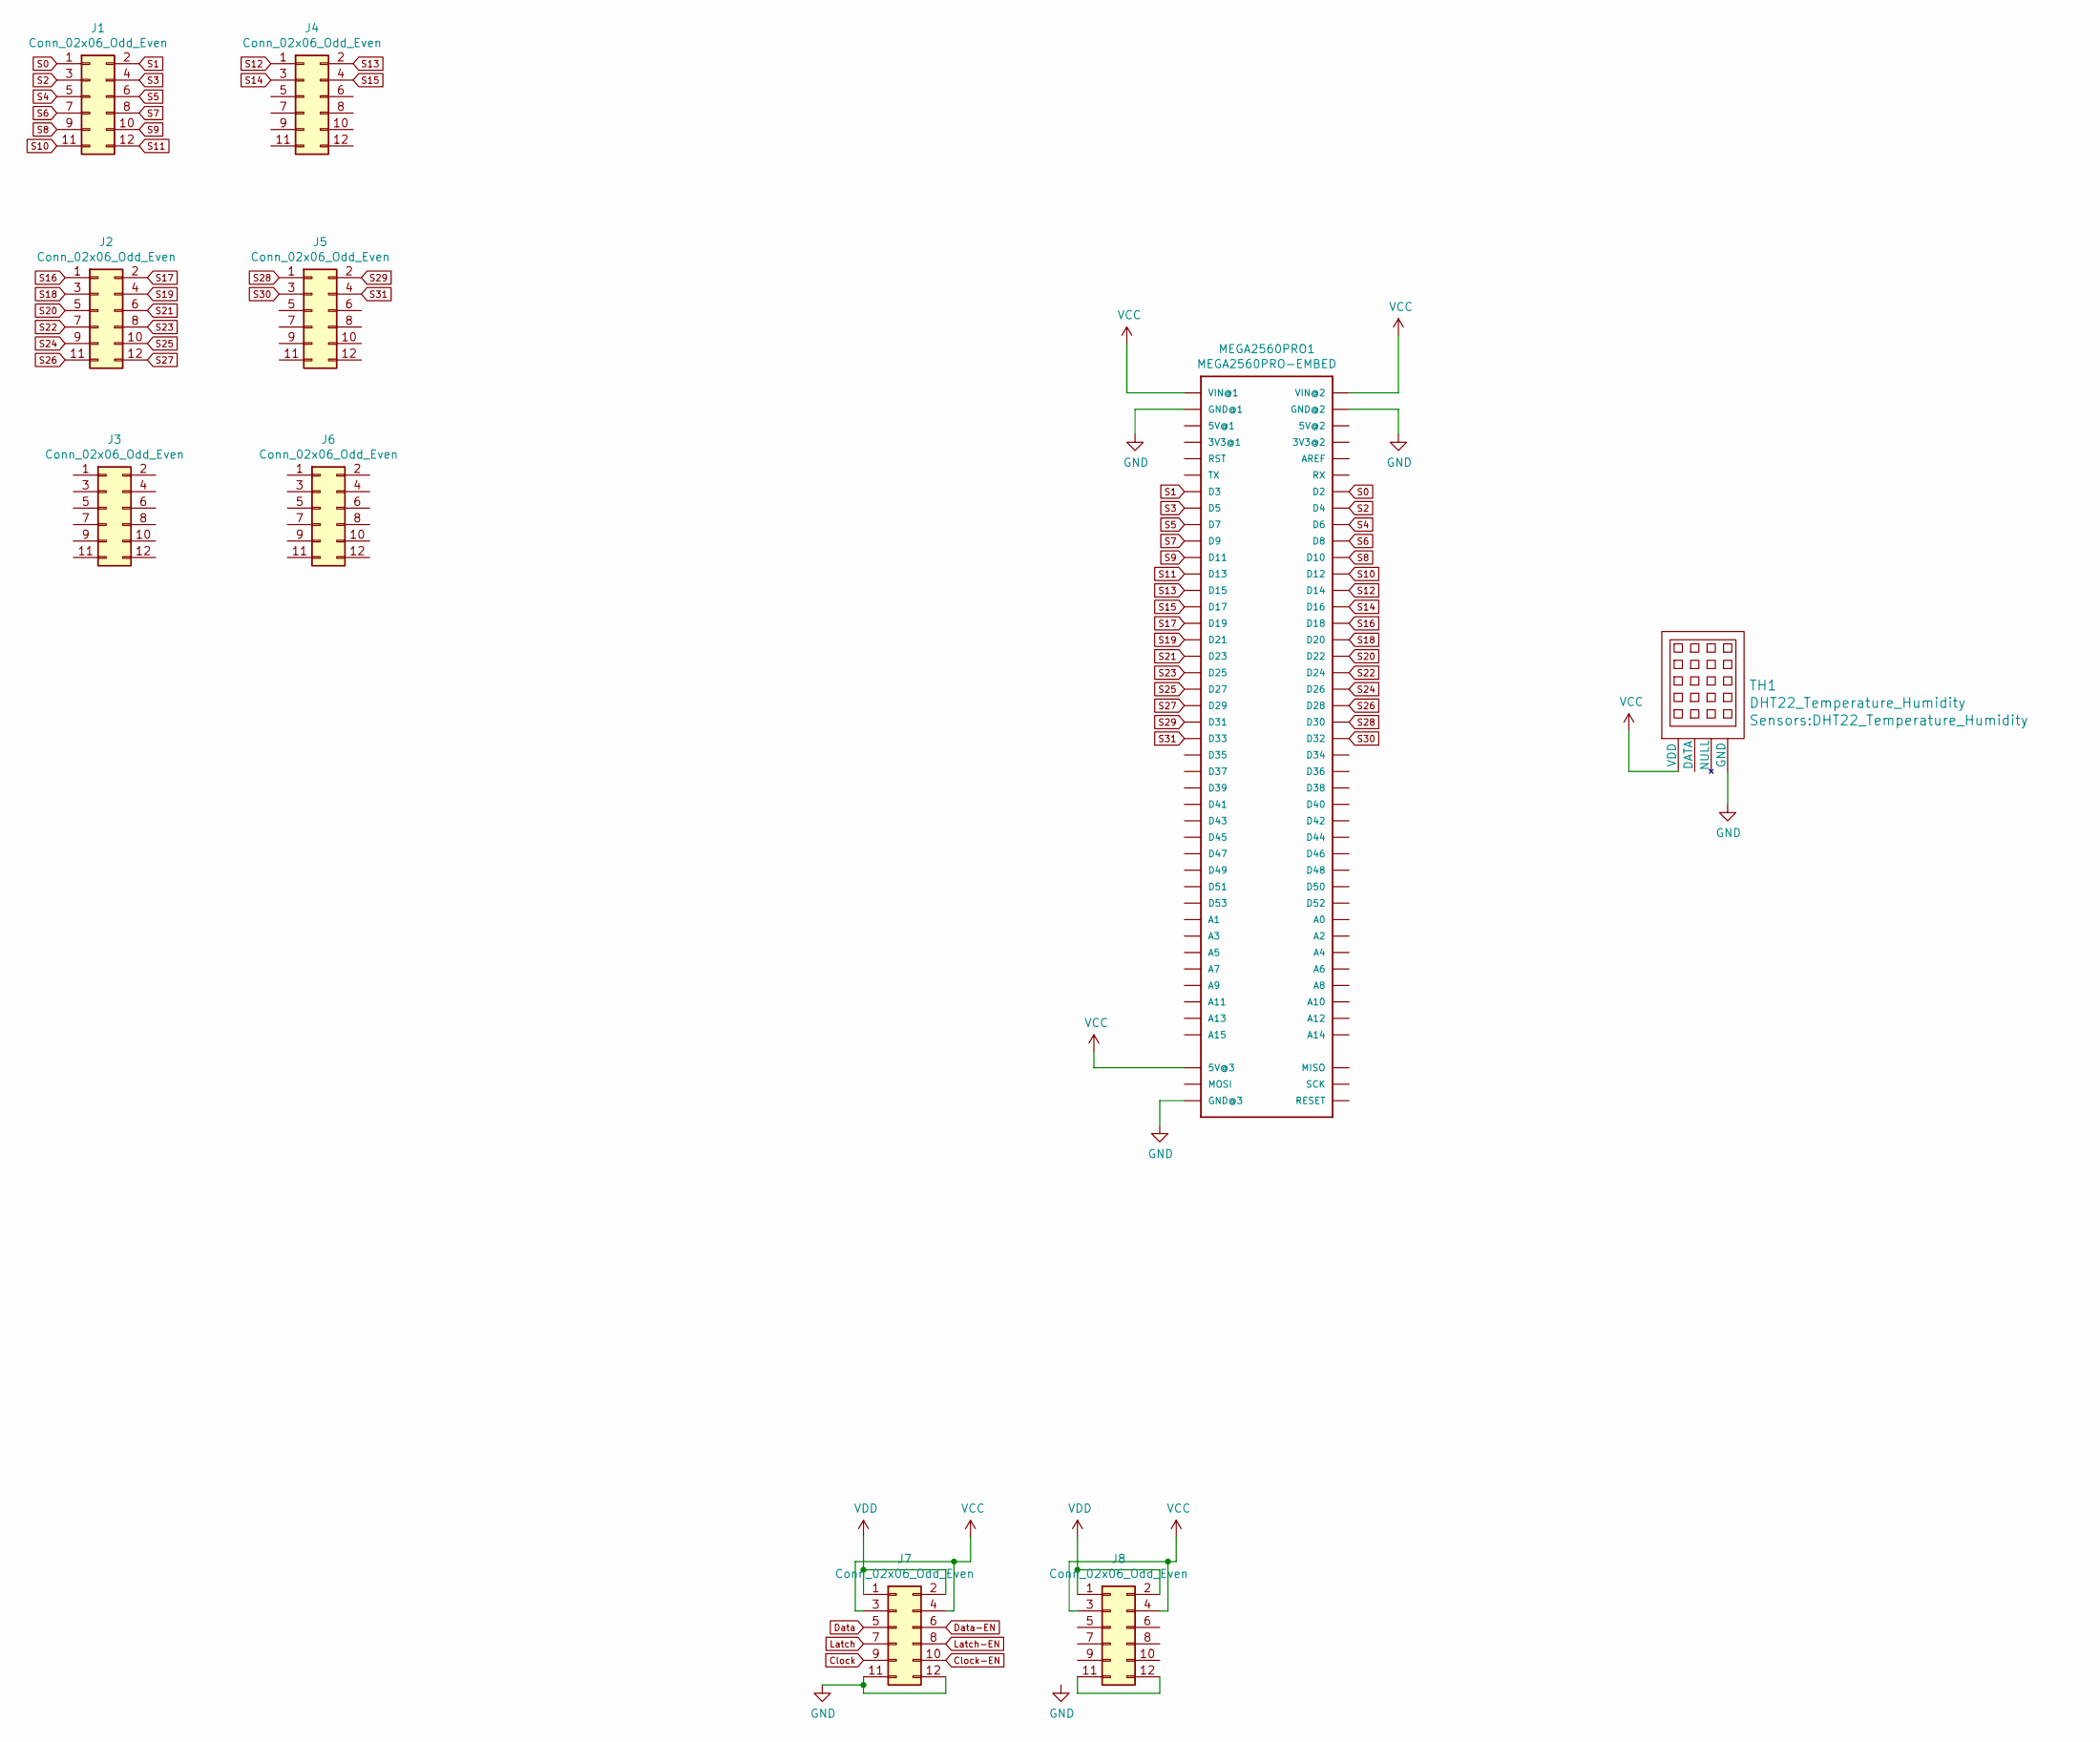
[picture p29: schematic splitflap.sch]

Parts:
J1, J2, J3, J4, J5, J6, J7, J8: Conn_02x06_Odd_Even; IDC-Header_2x06_P2.54mm_Vertical
MEGA2560PRO1: MEGA2560PRO-EMBED
TH1: DHT22_Temperature_Humidity

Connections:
Clock: J7.9
Clock-EN: J7.10
Data: J7.5
Data-EN: J7.6
GND: J7.11, J7.12, MEGA2560PRO1.GND@1, MEGA2560PRO1.GND@2, MEGA2560PRO1.GND@3, TH1.4 (GND)
Latch: J7.7
Latch-EN: J7.8
unnamed: J8.11, J8.12
S0: J1.1, MEGA2560PRO1.D2
S1: J1.2, MEGA2560PRO1.D3
S2: J1.3, MEGA2560PRO1.D4
S3: J1.4, MEGA2560PRO1.D5
S4: J1.5, MEGA2560PRO1.D6
S5: J1.6, MEGA2560PRO1.D7
S6: J1.7, MEGA2560PRO1.D8
S7: J1.8, MEGA2560PRO1.D9
S8: J1.9, MEGA2560PRO1.D10
S9: J1.10, MEGA2560PRO1.D11
S10: J1.11, MEGA2560PRO1.D12
S11: J1.12, MEGA2560PRO1.D13
S12: J4.1, MEGA2560PRO1.D14
S13: J4.2, MEGA2560PRO1.D15
S14: J4.3, MEGA2560PRO1.D16
S15: J4.4, MEGA2560PRO1.D17
S16: J2.1, MEGA2560PRO1.D18
S17: J2.2, MEGA2560PRO1.D19
S18: J2.3, MEGA2560PRO1.D20
S19: J2.4, MEGA2560PRO1.D21
S20: J2.5, MEGA2560PRO1.D22
S21: J2.6, MEGA2560PRO1.D23
S22: J2.7, MEGA2560PRO1.D24
S23: J2.8, MEGA2560PRO1.D25
S24: J2.9, MEGA2560PRO1.D26
S25: J2.10, MEGA2560PRO1.D27
S26: J2.11, MEGA2560PRO1.D28
S27: J2.12, MEGA2560PRO1.D29
S28: J5.1, MEGA2560PRO1.D30
S29: J5.2, MEGA2560PRO1.D31
S30: J5.3, MEGA2560PRO1.D32
S31: J5.4, MEGA2560PRO1.D33
VCC: J7.3, J7.4, J8.3, J8.4, MEGA2560PRO1.5V@3, MEGA2560PRO1.VIN@1, MEGA2560PRO1.VIN@2, TH1.1 (VDD)
VDD: J7.1, J7.2, J8.1, J8.2

Board: 2 copper layers, 10 parts (0 on the bottom side), 36 nets, no tracks yet.

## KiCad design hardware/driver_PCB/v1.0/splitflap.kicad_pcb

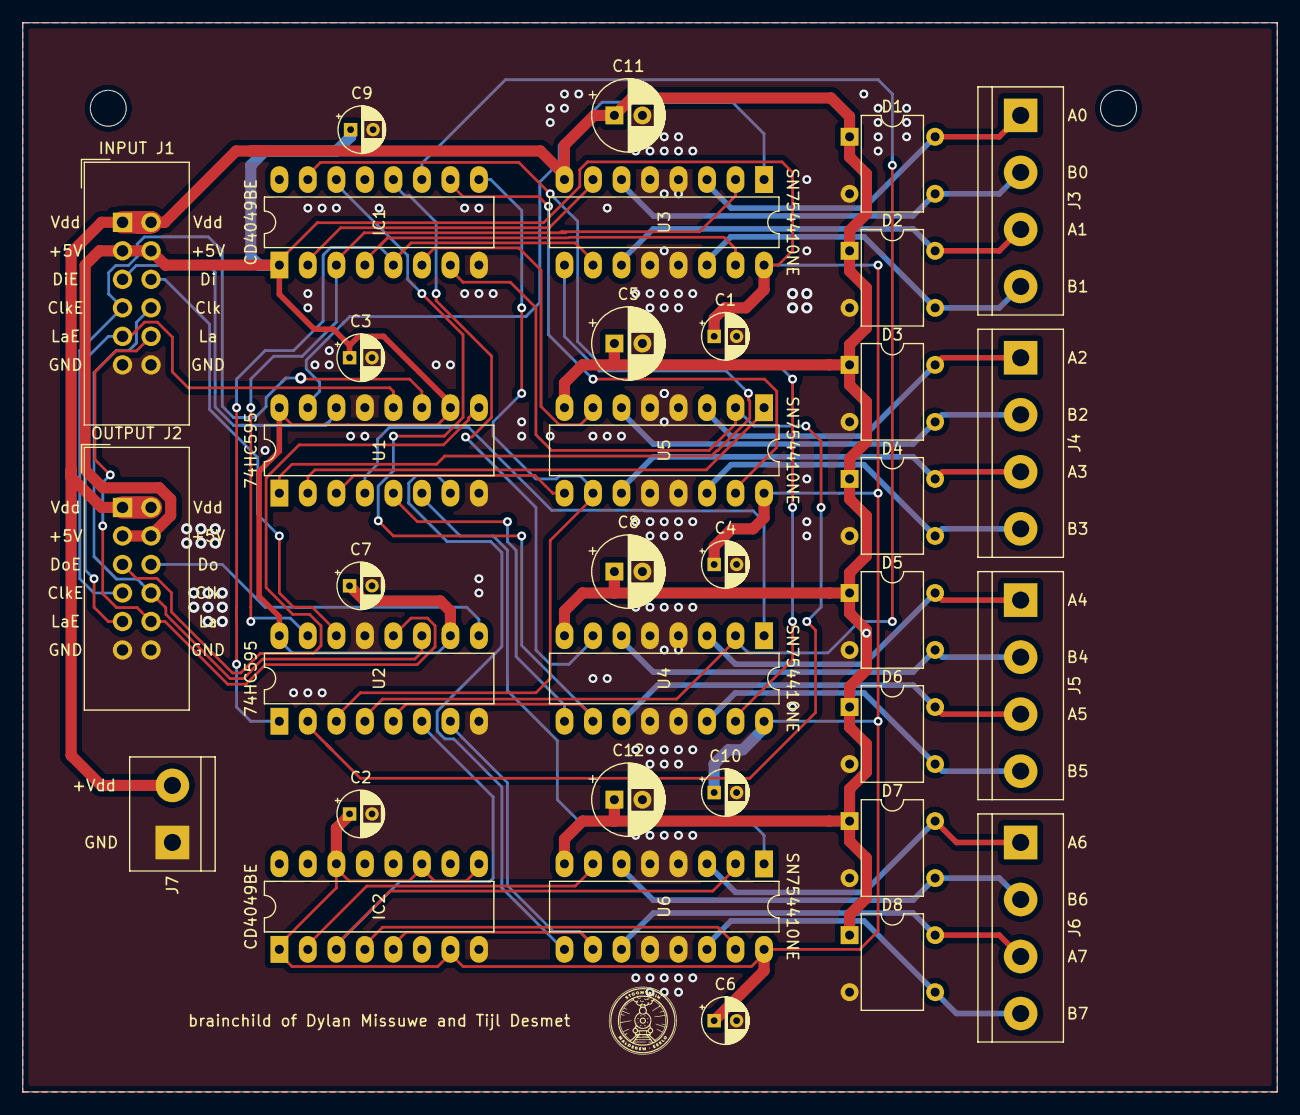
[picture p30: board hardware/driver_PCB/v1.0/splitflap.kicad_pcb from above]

Board: 2 copper layers, 111.8 x 95.2 mm, 35 parts (0 on the bottom side), 51 nets.

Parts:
C1, C2, C3, C4, C6, C7, C9, C10: CP; CP_Radial_D4.0mm_P2.00mm
C5, C8, C11, C12: CP; CP_Radial_D6.3mm_P2.50mm
D1, D2, D3, D4, D5, D6, D7, D8: D_Bridge_+-AA; Diode_Bridge_DIP-4_W7.62mm_P5.08mm
IC1, IC2: CD4049UBE; DIP-16_W7.62mm_LongPads
INPUT J1: Conn_02x06_Odd_Even; IDC-Header_2x06_P2.54mm_Vertical
J3, J4, J5, J6: Screw_Terminal_01x04; TerminalBlock_bornier-4_P5.08mm
J7: Screw_Terminal_01x02; TerminalBlock_bornier-2_P5.08mm
OUTPUT J2: Conn_02x06_Odd_Even; IDC-Header_2x06_P2.54mm_Vertical
U1, U2: 74HC595; DIP-16_W7.62mm_LongPads
U3, U4, U5, U6: SN754410NE; DIP-16_W7.62mm_LongPads

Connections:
GND: C1.2, C2.2, C3.2, C4.2, C5.2, C6.2, C7.2, C8.2, C9.2, C10.2, C11.2, C12.2, D1.2, D2.2, D3.2, D4.2, D5.2, D6.2, D7.2, D8.2, IC1.8, IC2.8, INPUT J1.11, INPUT J1.12, J7.1, OUTPUT J2.11, OUTPUT J2.12, U1.8, U1.13, U2.8, U2.13, U3.4, U3.5, U3.12, U3.13, U4.4, U4.5, U4.12, U4.13, U5.4, U5.5, U5.12, U5.13, U6.4, U6.5, U6.12, U6.13
unnamed: D1.3, J3.2, U3.6
unnamed: D1.4, J3.1, U3.3
unnamed: D2.3, J3.4, U3.14
unnamed: D2.4, J3.3, U3.11
unnamed: D3.3, J4.2, U5.6
unnamed: D3.4, J4.1, U5.3
unnamed: D4.3, J4.4, U5.14
unnamed: D4.4, J4.3, U5.11
unnamed: D5.3, J5.2, U4.6
unnamed: D5.4, J5.1, U4.3
unnamed: D6.3, J5.4, U4.14
unnamed: D6.4, J5.3, U4.11
unnamed: D7.3, J6.2, U6.6
unnamed: D7.4, J6.1, U6.3
unnamed: D8.3, J6.4, U6.14
unnamed: D8.4, J6.3, U6.11
unnamed: IC1.2, U3.7
unnamed: IC1.3, U2.15, U3.2
unnamed: IC1.4, U3.15
unnamed: IC1.5, U2.1, U3.10
unnamed: IC1.6, U5.7
unnamed: IC1.7, U2.2, U5.2
unnamed: IC1.9, U2.3, U5.10
unnamed: IC1.10, U5.15
unnamed: IC1.11, U2.4, U4.2
unnamed: IC1.12, U4.7
unnamed: IC1.14, U2.5, U4.10
unnamed: IC1.15, U4.15
unnamed: IC2.2, U6.7
unnamed: IC2.3, U2.6, U6.2
unnamed: IC2.4, U6.15
unnamed: IC2.5, U2.7, U6.10
unnamed: INPUT J1.5, U1.14
unnamed: INPUT J1.6, U2.14
unnamed: INPUT J1.7, OUTPUT J2.7, U1.11
unnamed: INPUT J1.8, OUTPUT J2.8, U2.11
unnamed: INPUT J1.9, OUTPUT J2.9, U1.12
unnamed: INPUT J1.10, OUTPUT J2.10, U2.12
unnamed: OUTPUT J2.5, U1.9
unnamed: OUTPUT J2.6, U2.9
unnamed: U1.1, U3.9
unnamed: U1.2, U5.1
unnamed: U1.3, U5.9
unnamed: U1.4, U4.1
unnamed: U1.5, U4.9
unnamed: U1.6, U6.1
unnamed: U1.7, U6.9
unnamed: U1.15, U3.1
VCC: C1.1, C2.1, C3.1, C4.1, C6.1, C7.1, C9.1, C10.1, IC1.1, IC2.1, IC2.7, IC2.9, IC2.11, IC2.14, INPUT J1.3, INPUT J1.4, OUTPUT J2.3, OUTPUT J2.4, U1.10, U1.16, U2.10, U2.16, U3.16, U4.16, U5.16, U6.16
VDD: C5.1, C8.1, C11.1, C12.1, D1.1, D2.1, D3.1, D4.1, D5.1, D6.1, D7.1, D8.1, INPUT J1.1, INPUT J1.2, J7.2, OUTPUT J2.1, OUTPUT J2.2, U3.8, U4.8, U5.8, U6.8

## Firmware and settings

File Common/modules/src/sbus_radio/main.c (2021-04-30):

#include <stdbool.h>
#include <stdio.h>
#include <string.h>
#include <fcntl.h>
#include <errno.h>
#include <unistd.h>
#include <sys/time.h>
#include <stropts.h>

#define termios asmtermios
#include <asm/termios.h>
#undef termios
#include <termios.h>

#include "sclog4c/sclog4c.h"
#include <lcm/lcm.h>

#include "lcm_channels.h"
#include "lcm/stomp_control_radio.h"

int time_diff_msec(struct timeval t0, struct timeval t1)
{
    return (t1.tv_sec - t0.tv_sec)*1000 + (t1.tv_usec - t0.tv_usec)/1000;
}

int main(int argc, char **argv)
{
    sclog4c_level = SL4C_FATAL; //default logging, fatal errors only
    const unsigned int sbus_baud = 100000;
    const int sbus_pkt_length = 25; //complete sbus packet size
    const int sbus_on_thresh = 1390;
    const int sbus_off_thresh = 590;
    const int sbus_max = 1811;
    const int sbus_min = 172;
    const float sbus_span = (sbus_max - sbus_min)/2.0f;
    const float sbus_center = (sbus_max + sbus_min)/2.0f;
    const int pkt_timeout_usec = 2000; //number of usecs to wait for serial data
    int sbus_timeout_msec = 500; //number of millis before calling SBUS dead

    int opt; //get command line args
    while((opt = getopt(argc, argv, "vt:")) != -1)
    {
        switch(opt)
        {
            case 'v': //v for verbose, set log level to debug
                sclog4c_level = SL4C_DEBUG;
                break;
            case 't':
                sbus_timeout_msec = atoi(optarg);
        }
    }

    struct timeval pkt_timeout;
    pkt_timeout.tv_sec = 0;
    pkt_timeout.tv_usec = pkt_timeout_usec;
    struct timeval last_send_time;
    struct timeval read_time;

    lcm_t *lcm = lcm_create(NULL);
    if(!lcm)
    {
        logm(SL4C_FATAL, "Failed to init LCM.");
        return 1;
    }
    stomp_control_radio lcm_msg;

    //open UART10
    int serial_port;
    serial_port = open("/dev/ttyS1", O_RDWR | O_NONBLOCK | O_NOCTTY);
    if (serial_port < 0)
    {
        logm(SL4C_FATAL, "Error %i from open(): %s", errno, strerror(errno));
        return 1;
    } else {
        logm(SL4C_DEBUG, "No error while opening port");
    }

    struct termios tty;
    memset(&tty, 0, sizeof tty); //create termios struct and set to zero
    if (tcgetattr(serial_port, &tty) != 0) //read current port config
    {
        logm(SL4C_WARNING, "Error %i from tcgetattr: %s", errno, strerror(errno));
    }

    tty.c_cflag |= PARENB;  //E
    tty.c_cflag |= CS8;     //8
    tty.c_cflag |= CSTOPB;  //2
    tty.c_cflag &= ~CRTSCTS; //disable hardware flow control
    tty.c_cflag |= CREAD | CLOCAL; //Turn on READ $ ignore ctrl lines

    tty.c_lflag &= ~ICANON; //non canonical
    tty.c_lflag &= ~ECHO; //disable echo
    tty.c_lflag &= ~ECHOE; //disable erasure
    tty.c_lflag &= ~ECHONL; //disable new-line echo
    tty.c_lflag &= ~ISIG; //disable interpretation of INTR, QUIT and SUSP

    tty.c_iflag &= ~(IXON | IXOFF | IXANY); //disable software flow control
    tty.c_iflag &= ~(IGNBRK|BRKINT|PARMRK|ISTRIP|INLCR|ICRNL); //disable special chars

    tty.c_oflag &= ~OPOST; //prevent special interpretation of output bytes
    tty.c_oflag &= ~ONLCR; //prevent nl converstion to cr

    tty.c_cc[VTIME] = 0; 
    tty.c_cc[VMIN] = 0;

    //try to set the configuration of the serial port
    if (tcsetattr(serial_port, TCSANOW, &tty) != 0)
    {
        logm(SL4C_WARNING, "Error %i from tcsetattr: %s", errno, strerror(errno));
    }

    //set custom baud rate
    struct termios2 tty2;
    ioctl(serial_port, TCGETS2, &tty2);
    tty2.c_cflag &= ~CBAUD;
    tty2.c_cflag |= BOTHER;
    tty2.c_ispeed = sbus_baud;
    tty2.c_ospeed = sbus_baud;
    if (ioctl(serial_port, TCSETS2, &tty2) < 0)
    {
        logm(SL4C_WARNING, "Error %i from ioctl: %s\n", errno, strerror(errno));
    }

    gettimeofday(&last_send_time, 0);
    while(true) //main loop, read sbus, then send data as lcm message
    {
        int pkt_length = 0;
        int num_bytes = 0;
        uint8_t sbus_pkt [256];
        uint8_t read_buff [256];
        memset(&sbus_pkt, '\0', sizeof(sbus_pkt));
        bool failsafe = true;
        bool good_packet = false;
        bool sbus_timeout = false;
        while(true) //packet read loop
        {
            fd_set rfds;
            FD_ZERO(&rfds);
            FD_SET(serial_port, &rfds);
            pkt_timeout.tv_usec = pkt_timeout_usec;
            int sret = select(serial_port + 1, &rfds, NULL, NULL, &pkt_timeout);
            if (sret > 0) //data available
            {
                memset(&read_buff, '\0', sizeof(read_buff));
                num_bytes  = read(serial_port, &read_buff, sizeof(read_buff));
                logm(SL4C_DEBUG, "Read returned with %i bytes", num_bytes);
                if (num_bytes > 0)
                {
                    int i;
                    for (i = 0; i < num_bytes; i++)
                    {
                        sbus_pkt[pkt_length] = read_buff[i];
                        pkt_length++;
                        if (pkt_length > sbus_pkt_length) break; 
                        //too many bytes
                    }

                } else {
                    logm(SL4C_WARNING, "Error %i from read: %s", errno, strerror(errno));
                }
            } else if (sret  == 0) { 
                //a valid SBUS packet must be followed by a select() timeout
                logm(SL4C_DEBUG, "Select() timeout occured");
                break; //break and check
            } else {
                logm(SL4C_WARNING, "Error %i from select %s", errno, strerror(errno));
            }

        } //end packet read loop;

        //check for sbus inactivity timeout first
        gettimeofday(&read_time, 0);
        int millis = time_diff_msec(last_send_time, read_time);
        if (millis > sbus_timeout_msec) 
        {
            logm(SL4C_DEBUG, "Timeout waiting for SBUS");
            sbus_timeout = true;
        } else if (pkt_length == sbus_pkt_length) {
            if (sbus_pkt[0] == 0x0F && sbus_pkt[24] == 0x00)
            {
                good_packet = true;
                logm(SL4C_DEBUG, "Complete SBUS packet received");
            } else {
                logm(SL4C_DEBUG, "Malformed SBUS packet received");
            } 
        }

        int axes = STOMP_CONTROL_RADIO_AXES;
        int toggles = STOMP_CONTROL_RADIO_TOGGLES;
        uint16_t sbus_raw[axes + toggles];
        memset(&sbus_raw, '\0', sizeof(sbus_raw));
        if (good_packet) //if pkt is good, process, otherwise set failsafe
        {
            //convert SBUS format into channel values as ints
            //low bits come in first byte, high bits in next byte, litte endian
            sbus_raw[0]  = (sbus_pkt[2]  << 8  | sbus_pkt[1])                           & 0x07FF; // 8, 3
            sbus_raw[1]  = (sbus_pkt[3]  << 5  | sbus_pkt[2] >> 3)                      & 0x07FF; // 6, 5
            sbus_raw[2]  = (sbus_pkt[5]  << 10 | sbus_pkt[4] << 2 | sbus_pkt[3] >> 6)   & 0x07FF; // 1, 8, 2
            sbus_raw[3]  = (sbus_pkt[6]  << 7  | sbus_pkt[5] >> 1)                      & 0x07FF; // 4, 7
            sbus_raw[4]  = (sbus_pkt[7]  << 4  | sbus_pkt[6] >> 4)                      & 0x07FF; // 7, 4
            sbus_raw[5]  = (sbus_pkt[9]  << 9  | sbus_pkt[8] << 1 | sbus_pkt[7] >> 7)   & 0x07FF; // 2, 8, 1
            sbus_raw[6]  = (sbus_pkt[10] << 6  | sbus_pkt[9] >> 2)                      & 0x07FF; // 5, 6
            sbus_raw[7]  = (sbus_pkt[11] << 3  | sbus_pkt[10] >> 5)                     & 0x07FF; // 8, 3
            sbus_raw[8]  = (sbus_pkt[13] << 8  | sbus_pkt[12])                          & 0x07FF; // 3, 8
            sbus_raw[9]  = (sbus_pkt[14] << 5  | sbus_pkt[13] >> 3)                     & 0x07FF; // 6, 5
            sbus_raw[10] = (sbus_pkt[16] << 10 | sbus_pkt[15] << 2 | sbus_pkt[14] >> 6) & 0x07FF; // 1, 8, 2
            sbus_raw[11] = (sbus_pkt[17] << 7  | sbus_pkt[16] >> 1)                     & 0x07FF; // 4, 7
            sbus_raw[12] = (sbus_pkt[18] << 4  | sbus_pkt[17] >> 4)                     & 0x07FF; // 7, 4
            sbus_raw[13] = (sbus_pkt[20] << 9  | sbus_pkt[19] << 1 | sbus_pkt[18] >> 7) & 0x07FF; // 2, 8, 1
            sbus_raw[14] = (sbus_pkt[21] << 6  | sbus_pkt[20] >> 2)                     & 0x07FF; // 5, 6
            sbus_raw[15] = (sbus_pkt[22] << 3  | sbus_pkt[21] >> 5)                     & 0x07FF; // 8, 3
            failsafe = sbus_pkt[23] & 0x08;
            lcm_msg.no_data = false;
        } else if (sbus_timeout) {
            failsafe = true;
            lcm_msg.no_data = true;
        } else {
            //only send an lcm message in the case of a good packet, or to send
            //failsafe=1 in the case of an sbus receive timeout
            continue;
        }

        int i;
        float sbus_axis[axes];
        for (i = 0; i < axes; i++)
        {
            sbus_axis[i] = (sbus_raw[i] - sbus_center)/sbus_span;
            lcm_msg.axis[i] = sbus_axis[i];
        }
        for (i = axes; i < (axes + toggles); i++)
        {
            int tog_i = i-axes;
            if (sbus_raw[i] > sbus_on_thresh) {
                lcm_msg.toggle[tog_i] = STOMP_CONTROL_RADIO_ON;
            } else if (sbus_raw[i] < sbus_off_thresh) {
                lcm_msg.toggle[tog_i] = STOMP_CONTROL_RADIO_OFF;
            } else {
                lcm_msg.toggle[tog_i] = STOMP_CONTROL_RADIO_CENTER;
            }
        }

        lcm_msg.failsafe = failsafe;
 
        logm(SL4C_DEBUG, "Channel 1: %i, Channel 2: %i, Failsafe: %i",
             sbus_raw[0], sbus_raw[1], failsafe);

        //send the lcm message, record time
        gettimeofday(&last_send_time, 0);
        stomp_control_radio_publish(lcm, SBUS_RADIO_COMMAND, &lcm_msg);
    }

    lcm_destroy(lcm);
    return 0;
}

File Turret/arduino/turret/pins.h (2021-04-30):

#ifndef PINS_H
#define PINS_H

// ----------------- ANALOG PINS ----------------- 

// Sensors

#define HAMMER_ANGLE_AI A1
#define HAMMER_THROW_PRESSURE_AI A3
#define HAMMER_RETRACT_PRESSURE_AI A5

// ----------------- DIGITAL PINS ---------------

//  Flame Thrower Control

#define PROPANE_LEFT_DO 2
#define PROPANE_RIGTH_DO 3
#define IGNITERS_DO 5

//  Hammer Control

//  VERY IMPORTANT: In HammerController.cpp there is optimized code that requires
//  these pin asignments DONT change.  Chaning just here will break things.  

//#define THROW_PRESSURE_VALVE_DO 6
//#define THROW_VENT_VALVE_DO 7
//#define RETRACT_PRESSURE_VALVE_DO 8
//#define RETRACT_VENT_VALVE_DO 9

//  Hammer Pressure
#define THROW_PRESSURE_VALVE_DO 6
#define RETRACT_PRESSURE_VALVE_DO 7

//  Hammer Vent
#define THROW_VENT_VALVE_DO 8
#define RETRACT_VENT_VALVE_DO 9

//  Hammer Enable
#define HAMMER_ENABLE_DO A8


//  XBee

#define XBEE_CTS_DI A12


// ----------------- SERIAL BUS (4 USRT & 1 I2C) ---------------

//  Just here so there is one place to know what pins are in use

//  UART 0
//  s_TelemetrySerial - Shared (one or the other) on-board USB and XBee raido
//  TX0 - DIGITAL PIN 1
//  RX0 - DIGITAL PIN 0

//  UART 1
//  s_TurretRotationMotorSerial - Roboteq Motor Contoller
//  TX1 - DIGITAL PIN 18
//  RX1 - DIGITAL PIN 19

//  UART 2
//  s_LeddarSerial - Leddar Depth / Distance Sensor
//  TX2 - DIGITAL PIN 16
//  RX2 - DIGITAL PIN 17

//  UART 3
//  FrSKY Remote Control Raido
//  TX3 - DIGITAL PIN 14
//  RX4 - DIGITAL PIN 15

//  I2C
//  s_IMUSerial - MPU6050 Inertial measurement unit (IMU)
//  SDA - DIGITAL PIN 20
//  SCL - DIGITAL PINT 21

// ----------------- GLOBALS ----------------

extern volatile bool g_enabled;

#endif

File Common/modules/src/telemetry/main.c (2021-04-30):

#include <inttypes.h>
#include <unistd.h>
#include <lcm/lcm.h>
#include <stdio.h>
#include <stdlib.h>
#include <sys/time.h>
#include <errno.h>

#include "messages.h"
#include "telemetry.h"
#include "lcm_channels.h"
#include "sbus_channels.h"
#include "lcm/stomp_control_radio.h"
#include "sclog4c/sclog4c.h"

#ifdef HULL
#include "lcm/stomp_telemetry_leg.h"
#endif

#ifdef TURRET
#include "lcm/stomp_turret_telemetry.h"
#include "lcm/stomp_sensors_control.h"
#endif

const int gnrl_period_msec = 200;  //general packet send period

#ifdef HULL
const int leg_period_msec = 200; //leg packet send period
#endif

#ifdef TURRET
const int turret_period_msec = 200; //turret packet send period
#endif

int time_diff_msec(struct timeval t0, struct timeval t1)
{
    return (t1.tv_sec - t0.tv_sec)*1000 + (t1.tv_usec - t0.tv_usec)/1000;
}

static void sbus_handler(const lcm_recv_buf_t *rbuf, const char *channel,
                       const stomp_control_radio *msg, void *user)
{
    static struct timeval now;
    static struct timeval last_send_time;

    gettimeofday(&now, 0);
    logm(SL4C_DEBUG, "Received message on channel %s, at %ld.%ld\n", channel, now.tv_sec, now.tv_usec);
    logm(SL4C_DEBUG, "Data size: %d\n", rbuf->data_size);
 
    logm(SL4C_DEBUG, "  failsafe:%i\n", msg->failsafe);
    logm(SL4C_DEBUG, "  no_data:%i\n", msg->no_data);
    gettimeofday(&now, 0);
    int millis = time_diff_msec(last_send_time, now);
    if (millis > 1000)
    {
    }
}

#ifdef HULL

int8_t m_to_int(float value){
    return (int8_t) value;
}

int8_t psi_to_int(float value){
    return (int8_t) value;
}

static void leg_handler(const lcm_recv_buf_t *rbuf, const char *channel,
                       const stomp_telemetry_leg *msg, void *user)
{
    static struct timeval now;
    static struct timeval last_send_time;

    gettimeofday(&now, 0);
    int millis = time_diff_msec(last_send_time, now);
    logm(SL4C_DEBUG, "%d msec since last %s msg received", millis, channel);

    if (millis > leg_period_msec) //prepare and send COSMOS msg
    {
        gettimeofday(&last_send_time, 0);
        struct legs_cosmos cosmos_msg;
        logm(SL4C_DEBUG, "Sending COSMOS LEGS packet");
        int leg;
        for (leg = 0; leg < STOMP_TELEMETRY_LEG_LEGS; leg++)
        {
            int curl = leg + STOMP_TELEMETRY_LEG_CURL;
            int swing = leg + STOMP_TELEMETRY_LEG_SWING;
            int lift = leg + STOMP_TELEMETRY_LEG_LIFT;
            cosmos_msg.curl_base_psi[leg] = psi_to_int(msg->base_end_pressure[curl]);
            cosmos_msg.curl_rod_psi[leg] = psi_to_int(msg->rod_end_pressure[curl]);
            cosmos_msg.swing_base_psi[leg] = psi_to_int(msg->base_end_pressure[swing]);
            cosmos_msg.swing_rod_psi[leg] = psi_to_int(msg->rod_end_pressure[swing]);
            cosmos_msg.lift_base_psi[leg] = psi_to_int(msg->base_end_pressure[lift]);
            cosmos_msg.lift_rod_psi[leg] = psi_to_int(msg->rod_end_pressure[lift]);
            cosmos_msg.toe_pos_x[leg] = m_to_int(msg->toe_position_measured_X[leg]);
            logm(SL4C_DEBUG, "Leg: %d, toe_x_pos: %.4f, cosmos: %d", leg, msg->toe_position_measured_X[leg], cosmos_msg.toe_pos_x[leg]);
            cosmos_msg.toe_cmd_x[leg] = m_to_int(msg->toe_position_commanded_X[leg]);
            cosmos_msg.toe_pos_y[leg] = m_to_int(msg->toe_position_measured_Y[leg]);
            cosmos_msg.toe_cmd_y[leg] = m_to_int(msg->toe_position_commanded_Y[leg]);
            cosmos_msg.toe_pos_z[leg] = m_to_int(msg->toe_position_measured_Z[leg]);
            cosmos_msg.toe_cmd_z[leg] = m_to_int(msg->toe_position_commanded_Z[leg]);
        }
        cosmos_msg.observed_period = (uint8_t) (msg->observed_period*1000);
        telem_publish(LEGSTAT, (char *)&cosmos_msg, sizeof(cosmos_msg));
    }
}

#endif

#ifdef TURRET

static void turret_telemetry_handler(const lcm_recv_buf_t *rbuf, const char *channel,
                       const stomp_turret_telemetry *msg, void *user)
{
    static struct timeval now;
    static struct timeval last_send_time;

    gettimeofday(&now, 0);
    int millis = time_diff_msec(last_send_time, now);
    logm(SL4C_DEBUG, "%d msec since last %s msg received", millis, channel);

    if (millis > turret_period_msec) //prepare and send COSMOS msg
    {
        gettimeofday(&last_send_time, 0);
        struct turret_gnrl_cosmos cosmos_msg;
        logm(SL4C_DEBUG, "Sending COSMOS Turret General packet");

        cosmos_msg.turret_state = msg->turret_state;

        telem_publish(TURRET_GNRL, (char *)&cosmos_msg, sizeof(cosmos_msg));
    }
}

static void turret_sensors_control_handler(const lcm_recv_buf_t *rbuf, const char *channel,
                       const stomp_sensors_control *msg, void *user)
{
    static struct timeval now;
    static struct timeval last_send_time;

    gettimeofday(&now, 0);
    int millis = time_diff_msec(last_send_time, now);
    logm(SL4C_DEBUG, "%d msec since last %s msg received", millis, channel);

    if (millis > turret_period_msec) //prepare and send COSMOS msg
    {
        gettimeofday(&last_send_time, 0);
        struct turret_sensors_cosmos cosmos_msg;
        logm(SL4C_DEBUG, "Sending COSMOS Turret Sensors packet");

        cosmos_msg.hammer_angle = msg->hammer_angle;
        cosmos_msg.turret_angle = msg->turret_angle;
        cosmos_msg.throw_pressure = msg->throw_pressure;
        cosmos_msg.retract_pressure = msg->retract_pressure;

        telem_publish(TURRET_SNS, (char *)&cosmos_msg, sizeof(cosmos_msg));
    }
}

#endif

int main(int argc, char **argv)
{
    sclog4c_level = SL4C_FATAL; //default logging, fatal errors only
    telem_init();

    int opt; //get command line args
    while((opt = getopt(argc, argv, "vt:")) != -1)
    {
        switch(opt)
        {
            case 'v': //v for verbose, set log level to debug
                sclog4c_level = SL4C_DEBUG;
                break;
        }
    }

    lcm_t *lcm = lcm_create(NULL);
    if (!lcm)
    {
        logm(SL4C_FATAL, "Failed to init LCM.");
        return 1;
    }

    stomp_control_radio_subscribe(lcm, SBUS_RADIO_COMMAND, &sbus_handler, NULL);

#ifdef HULL
    stomp_telemetry_leg_subscribe(lcm, LEG_TELEMETRY, &leg_handler, NULL);
#endif

#ifdef TURRET
    stomp_turret_telemetry_subscribe(lcm, TURRET_TELEMETRY, &turret_telemetry_handler, NULL);
    stomp_sensors_control_subscribe(lcm, SENSORS_CONTROL, &turret_sensors_control_handler, NULL);
#endif

    while (1)
    {
        int lcm_fd = lcm_get_fileno(lcm);
        fd_set fds;
        FD_ZERO(&fds);
        FD_SET(lcm_fd, &fds);
        logm(SL4C_DEBUG, "Waiting forever for LCM message");
        int status = select(lcm_fd + 1, &fds, 0, 0, NULL);
        if (status <= 0 ){
            logm(SL4C_FATAL, "Error %i from select(): %s", errno, strerror(errno));
        } else {
            lcm_handle(lcm);
        }
    }

    lcm_destroy(lcm);
    return 0;
}

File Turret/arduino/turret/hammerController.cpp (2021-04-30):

//
//  Hammer Controller
//
//  Throw (or swing) the hammer with pneumatic valve open for a period of
//  of time, then close that valve and the the throw continue.  Then retract
//  the hammer and get ready for another throw.
//
//  This is accomplished with 4 valves to control pneumatics: 
//
//      Throw Pressure, Throw Vent, Retract Pressure, Retract Vent
//
//  Due to the strict and short timing requirements, the valve control
//  and hammer angular velocity calculations are handled in an 
//  interrupt driven state machine, implemented at the end of this file
//  after the class method implementation
//

#include "Arduino.h"
#include <avr/interrupt.h>
#include <util/atomic.h>
#include "pins.h"

#include "sbus.h"
#include "DMASerial.h"

#include "turretController.h"
#include "telemetryController.h"
#include "radioController.h"

#include "hammerController.h"

#include "sensors.h"


//  ====================================================================
//
//  External references
//
//  ====================================================================

extern volatile bool sbus_weaponsEnabled;

//  ====================================================================
//
//  File constants 
//
//  ====================================================================

static const int16_t k_invalidHammerAngleRead = -1;
static const int16_t k_invalidHammerThrowPressureRead = -1;
static const int16_t k_invalidHammerRetractPressureRead = -1;

//  ====================================================================
//
//  File static variables
//
//  ====================================================================

static struct HammerController::Params EEMEM s_savedParams = 
{
    .selfRightIntensity = 30,
    .swingTelemetryFrequency = 400,
    .maxThrowAngle = 2966,
    .minRetractAngle = 87,
    .emergencyBrakeAngle = 1047,               //  60 degrees as milliradians
    .throwSideBrakingForceTrigger = 0.005102f, // s^2
    .brakeStopAngle = 87.3f,                   // mrad
    .maxThrowUnderPressureDt = 750000,         // us
    .maxThrowExpandDt = 250000,                // us
    .maxRetractUnderPressureDt = 1000000,      // us
    .maxRetractExpandDt = 1000000,             // us
    .maxRetractBrakeDt = 1000000,              // us
    .maxRetractSettleDt = 500000,              // us
    .minBrakeExitVelocity = -872,              //mrad/sec
    .retractFillPressure = 448,                // kPa
};


static uint16_t s_telemetryFrequency;

volatile static bool s_swingComplete;

//  These are file static rather than member variables because they are 
//  being accesses from an interrupt service routing

volatile static int16_t s_hammerAngleCurrent = k_invalidHammerAngleRead;
volatile static int32_t s_hammerVelocityCurrent = 0;
volatile static int32_t s_hammerAngleReadTimeLast = 0;
volatile static int32_t s_hammerVelocityFilter = 0;

volatile static int16_t s_hammerThrowPressureCurrent = k_invalidHammerThrowPressureRead;
volatile static int16_t s_hammerRetractPressureCurrent = k_invalidHammerRetractPressureRead;

volatile static int16_t s_hammerThrowAngle = 0;

volatile static int16_t s_maxThrowAngle;
volatile static int16_t s_minRetractAngle;
volatile static int16_t s_emergencyBrakeAngle;
volatile static float s_throwSideBrakingForceTrigger;
volatile static float s_brakeStopAngle;
volatile static uint32_t s_maxThrowUnderPressureDt;
volatile static uint32_t s_maxThrowExpandDt;
volatile static uint32_t s_maxRetractUnderPressureDt;
volatile static uint32_t s_maxRetractExpandDt;
volatile static uint32_t s_maxRetractBrakeDt;
volatile static uint32_t s_maxRetractSettleDt;
volatile static int32_t s_minBrakeExitVelocity;
volatile static int32_t s_retractFillPressure;

//  ====================================================================
//
//  Forward references to internal (private) methods
//
//  ====================================================================

void startFullCycleStateMachine();
void startRetractOnlyStateMachine();
void startSensorReadStateMachine();

void swingComplete();

//  ====================================================================
//
//  Constructors
//
//  ====================================================================

//  ====================================================================
//
//  Public API methods
//
//  ====================================================================

void HammerController::Init()
{
    m_state = EInvalid;
    m_lastUpdateTime = micros();
    setState(EInit);
}

void HammerController::Update()
{
    m_lastUpdateTime = micros();

    //  Pass update to our owned objects

    //  Update our state

    while(true)
    {
        controllerState prevState = m_state;

        switch (m_state)
        {
            case EInit:
            {
                setState(ESafe);
            }
            break;

            case ESafe:
            {
                //  Stay in safe mode for a minimum of k_safeStateMinDt

                if (m_lastUpdateTime - m_stateStartTime > k_safeStateMinDt && Radio.IsNominal())
                {
                    if (isWeaponEnabled())
                    {
                        setState(EReady);
                    }
                    else
                    {
                        setState(EDisabled);
                    }
                }
            }
            break;

            case EDisabled:
            {
                if (!Radio.IsNominal())
                {
                    setState(ESafe);
                }
                else if (isWeaponEnabled())
                {
                    setState(EReady);
                }
            }
            break;

            case EReady:
            {
                if (!Radio.IsNominal())
                {
                    setState(ESafe);
                }
                else if (!isWeaponEnabled())
                {
                    setState(EDisabled);
                }
            }
            break;

            case EFullCycleInterruptMode:
            case ERetractOnlyInterruptMode:
            {
                if (s_swingComplete)
                {
                    //Telem.LogMessage("Swing Complete");
                    setState(ESwingComplete);
                }
            }
            break;

            case ESwingComplete:
            {
                setState(EReady);
            }
            break;

            default:
            break;
        }

        //  No more state changes, move on

        if (m_state == prevState)
        {
            break;
        }
    }

    //  Now that the state is stable, take action based on stable state
}

void HammerController::Safe()
{
    setState(ESafe);
}

bool HammerController::ReadyToSwing()
{
    return m_state == EReady;
}

bool HammerController::IsSafeForFlameThrowers()
{
    return m_state == EReady;
}
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

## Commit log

2020-01-13 Meshes and inertia for leg components
    [Leg 1 Foot Simplified.obj, Leg 1 Hip Simplified.obj, Leg 1 Thigh Simplified.obj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]
2020-01-13 Start wiring diagram, pick some connectors.
    [Platform.kicad_pcb, Platform.sch]
2020-01-15 Add more connectors, leg board
    [LegBoard.sch, Platform.sch]
2020-01-15 Connector updates
    Change S2 cable to pre-made set
    Add power connectors
    [LegBoard.sch, Platform.sch]
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2020-01-19 Switch Leg Board connectors
    [LegBoard.sch, Platform.sch]
2020-01-20 Update to show all legs on block diagram
    Add radios to platform diagram
    [Leg.sch, LegBoard.sch, Platform.sch]
2020-01-21 Start power distribution
    [BaterySled.sch, Leg.sch, LegBoard.sch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]
2020-01-22 More platorm parts and connectors
    [BaterySled.sch, Platform.sch, PowerDistribution.sch]
2020-01-23 Added Digikey part numbers for 3-pin
    [LegBoard.sch]
2020-01-29 Add skeleton for LegBoard firmware
    Move README into new LegBoard directory
    Add template for STM32F277 project
2020-01-30 Just a leg
    [Leg.urdf]
2020-02-01 Updates to simulator
    [Stomp.xacro]
2020-02-05 Initial commit of leg board PCB project.
    [Analog.SchDoc, Connectors.SchDoc, LEDs.SchDoc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]
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2020-02-10 Initial port of chomp's code, pared down to represent the new turret control. This all complies and works on the systems we removed from chomp. The eeprom section doesn't seem to get flashed to the a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
    [pins.h, turret.ino]
2020-02-12 Adjust electronics hierarchy to match mechanicals.
    [BaterySled.sch, ElectronicsModule.sch, Leg.sch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]
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2020-02-14 Initial commit for cosmos (for the turret). No real changes, just getting a base version checked in before I start mucking it up.
    [ConfigTables_def.txt, MCConfigurationTable_fsw1_def.txt, MCConfigurationTable_fsw2_def.txt]
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2020-02-16 Update part numbers for BOM generation
    [BaterySled.sch, ElectronicsModule.sch, Leg.sch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]
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2020-02-19 Switch back to `722 for more memory
    And more hacking on linearization
2020-02-19 Blinky lights on '722 dev board
    Remove once I get real hardware
2020-02-19 Fix compile warning
    Variable type doesn't really matter here since we just need the address
    to know what block of data to copy from flash to RAM.
    [storage.c]
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2020-02-28 Do as I say not as I do.
    Giant dump of much too much work.
    Working LED demo on real board.
    Lots of work on UARTS/modbus.
    New linker script, smaller image.
    [feedback_adc.c, feedback_adc.h, linearize_feedback.c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]
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2020-02-28 Move leg board schematics and firmware into one tree
    [Analog.SchDoc, Connectors.SchDoc, LEDs.SchDoc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]
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2020-03-05 Fix interrupt and taks priorities
    [enfield.c, linearize_feedback.c, modbus.c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]
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2020-03-05 Always clear uart error flags
    and only report if the interrupt was requested
2020-03-05 Use joint angle enum correctly
    [feedback_adc.c, linearize_feedback.c, main.c]
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2020-03-08 Revert "Move UART6 DMA away from ADC"
    This reverts commit e170a18877dbe8689c2231ad71644dc1a8654493.
    [enfield_uart.h]
2020-03-08 Correct size for storage pointers
    [storage.c]
2020-03-08 Fix UART DMA setup
2020-03-08 Better understanding of Enfield protocol
    Correct some messages, decode a few more
    [enfield.c, enfield.h]
2020-03-09 Adjust modbus internal API
    Allow for error code return value.
    [enfield.c, linearize_feedback.c, modbus.c]
2020-03-09 Fix Enfield state machine
    Set command to digital on startup
    Correct state transitions around execute/sample
    [enfield.c]
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2020-03-09 Correct command ids for area ratio and bore
    [enfield.h]
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2020-03-10 Move modbus thread state to static allocation
    Stack allocation was causing an overflow.
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2020-03-10 Better enfield state management
    Fewer stack-allocated values, might work with multiple servos now.
    Handle command requests before init.
2020-03-10 Fix error handling bugs
    [modbus.c]
2020-03-11 Correct LED brightness scaling
    [linearize_feedback.c]
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2020-03-11 Handle UART errors during timeout interrupt
2020-03-11 Record errors during enfield loop
    Only save result if no error
    [enfield.c]
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2020-03-12 Correct some geometry values
    [linearize_feedback.c]
2020-03-12 Record errors during enfield update
    [enfield.c]
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2020-03-13 Correct angle linearization constants
    [linearize_feedback.c]
2020-03-14 Move kinematics into its own file
    And add toe position -> joint angles code
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2020-03-22 Early steps on Hammer controller's interrupt driven state machine. A ways still to go, but heading out to the shop again and wanted to get everything checked in. Also tweaking AutoAim for more testing
2020-03-22 Revert "Add UART Receive timeout to HAL"
    This reverts commit b5787b8a092741b1fde174740e04379251b234c0.
2020-03-27 Feel really good about where HammerController is. Have Timer Interrupt setup and ISR for state machine implemented. Have done no testing on this yet, and not read for hammer angle yet. But good to ge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
2020-04-04 Tweaks to Hammer Controller and a new Fixed Point full PID impl for auto aim. Going out to shop to test it all out.
    [hammerController.cpp, pins.h]
2020-04-20 Cleaning up a bug around calls to micros() in the same update loop will actually show time passing. For correct state machine operation, time should be sampled at start of state machine update and us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
    [flameThrowerController.cpp, hammerController.cpp]
2020-05-29 In the middle of cleaning up TurretController state machine. Lots of little things. The TelemetryController is setup to allow "printf" debugging over the normal serial connection without XBee. Like "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
    Going out to shop to test, so I want to check everything in so I can work from my laptop.
2020-06-07 Fixed issue where hammerSwing interrupt frequency was too great so serial writes to the RoboteQ were failing. Can now swing hammer and rotate turret at the same time. Also still working on TelemetryC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
    [hammerController.cpp, telemetryController.cpp]
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2020-06-13 Better error handling in enfield comm
    [enfield.c]
2020-06-13 PINF debugging for enfield update
    Set a pin when a new value is sent to the enfield, checking regular
    update period.
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2020-06-15 Correct pointer type in kinematics
    Interaction with modbus needs unsigend pointers
2020-06-15 Add errno implementation
    Normally provided by newlib, use FreeRTOS thread local storage.
2020-06-16 Tighten up timing in enfield loop
    Try to exactly meet sample_rate by checking elapsed time
    [enfield.c]
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2020-06-16 Switch back to immediate enfield write
    Cached write has too many timing problems
2020-06-17 Switch to newlib errno implementation
    This took too long to figure out, but this is the correct errno
    solution. Need larger malloc heap for reentrant structure.
    [main.c]
2020-06-17 MODBUS control of sensor constants
    Rename for clarity.
    Split structure for more natural control.
    Add messages to get/set sensor limits.
    Recompute scale/offset on init and on set.
2020-06-20 Correct printf format
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2020-06-21 Fix flash layout and storge writeback
    [storage.c]
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2020-06-25 Fix timer sleep
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2020-06-26 Fix minmax mode for sensor calibration
2020-06-27 Try ping again when enfield command fails
    [enfield.c]
2020-06-27 Flush receive buffer on Enfield CRC error
    [enfield.c]
2020-06-27 Retry gain setting on server failure
    [simple_gait.c]
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2020-06-28 Converting analogReads for all "sensors" into an interrupt driven system. Code is now in hammerController (at least for now).
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2020-07-05 Fixed up silly mistakes in hammer controller. All good now.
    [hammerController.cpp]
2020-07-12 Cleaning up any (most) compiler warning and getting all telemetry correct between cosmos and arduino (first pass, going to do deeper code reviews in the not to distant future).
    [flameThrowerController.cpp, hammerController.cpp, telemetryController.cpp]
2020-07-15 Fix leg phase
2020-07-15 Correct phase startup
    modf can return -0.0, confuses interpolation.
    [simple_gait.c]
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2020-07-19 Fix input initialization in sensor display
2020-07-19 Missing cylinder pivot
2020-07-19 Fix linearization length scale
    [linearize_feedback.c]
2020-07-19 imu.cpp to imuController.cpp controller object pattern. Want to get this all checked in as I move on to getting auto fire to work.
2020-07-20 Fix JointAngle order
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2020-07-24 Flip legs on other side
    [simple_gait.c]
2020-07-24 Fix DMA receive error handling
    Likely removed while debugging DMA, oops
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2020-08-07 Some more work on the AutoFireController. Fix up some of the PID default values for AutoAimController. Get the TargetTrackingController "WillHitTrackedTarget()" method implemented. start writing thin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
    [flameThrowerController.cpp]
2020-08-08 WIP leg control thread
    Still building out leg control path, builds but nowhere near complete.
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2020-08-11 Fixed another issue with m_pBestTarget not being NULL when it should. Also getting additional telemetry over to Cosmos.
    [telemetryController.cpp]
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2020-08-15 Better error handling in leg feedback
2020-08-15 Switch to correct mode when stop requested
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2020-08-16 Fix leg control frequency specification
    [main.c]
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2020-08-16 Fixed axis and toggle definitions, and usage
    [main.c]
2020-08-16 Trying new target acquisition / segmentation idea to try and keep track of targets that were in the Leddar FOV but have just moved off to one side or another.
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2020-08-20 As built files
    [Analog.SchDoc, LEDs.SchDoc, LegBoard.PcbDoc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]
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2020-08-28 Initial addition of BeagleCape files. Will be generating fab files for quote to be added in a subsequent commit.
    [ADC.SchDoc, ADCClick.SchDoc, BEAGLEBONEBLACK_REV A5B.PrjPcb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]
2020-08-29 remove, now outdated, Turret/cosmos
    [ConfigTables_def.txt, MCConfigurationTable_fsw1_def.txt, MCConfigurationTable_fsw2_def.txt]
2020-08-29 Clean up error handling
    Always reset error state every loop.
    [enfield.c]
2020-08-29 Only save feedback value if no errors
    [enfield.c]
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2020-08-30 Partial implementation of MODBUS_DIAGNOSTICS
    Just the error counters for now.
    [modbus.c]
2020-09-02 Fix printing nested arrays of tables
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2020-09-03 Remove int64_t, hard to print on 32bit and 64bit
    And add address to error messages
2020-09-03 Fix single-leg calibration
2020-09-07 Slow down Enfield communicaiton
    And add pause around recovery state. This seems to help with loss of
    communicaiton, sending packets too quickly is problematic.
    [enfield.c]
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2020-09-08 Re-order interrupt enables
    Enable DMA early to prevent bad exit condition.
    Clear all error flags before enabling error interrupt
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2020-09-08 Clean up modbus error counters
    [modbus.c]
2020-09-08 Better modbus receive/transmit setup
    Use Abort to clean up if an error occurs during a request.
    Move timeout setup to before request to ensure proper clenaup if an
    error occurs early in reception.
    [modbus.c]
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2020-09-10 Fixed bug is keeping track of target edges (and therefore size calculations). Getting ready to go get some more telemetry data so cleaning up so output.
2020-09-10 Remove cosmos folder in Turret
    [ConfigTables_def.txt, MCConfigurationTable_fsw1_def.txt, MCConfigurationTable_fsw2_def.txt]
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2020-09-11 Added logging and corrected string format
    [main.c]
2020-09-12 Fix queue checking in mainloop
    Faster.
    Always, even after handling messages.
    [main.c]
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2020-09-12 Fix leg rotation multiply
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2020-09-13 Loosen leg positioning tolerance
2020-09-13 More debug output to figure out leddar issues when lots of detections exist
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2020-09-15 V0 as fabbed files. BOM has not been ordered/verified.
    [ADC.SchDoc, BMS.SchDoc, BeagleCape.PcbLib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]
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2020-09-16 Cleaned up BOM. Files are as ordered for rev 0 board assembly.
    [ADC.SchDoc, BMS.SchDoc, BeagleCape.PrjPcb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]
2020-09-16 Per-leg direction swap
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2020-09-20 Correct all legs, not just loaded ones
    And correct to new desired plus error term
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2020-09-20 Adding UserGuide for leddar I found while trying to debug issue.
2020-09-20 Clean up compile warnings (which exposed a few errors). Clearly I need to use Make to build.
    [imuController.cpp, telemetryController.cpp]
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2020-09-29 - Add Roboteq config file for new brushless turret motor - Cleaning up Turret Controller state machine - Remove some of my debug logging trying to find leddar serial error - Added some more safety co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
    [imuController.cpp, telemetryController.cpp, turret.ino]
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2020-10-03 Fix Nasty Array Overrun bug.
    [hammerController.cpp]
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2020-10-04 Get velocity into the correct degrees / second for display
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2020-10-04 Fix hammer vleocity scaling calculation
    [hammerController.cpp]
2020-10-04 Correct conversion for hammer velocity
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2020-10-04 Correct brake condition and remove divide by zero
    [hammerController.cpp]
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2020-10-05 Fix brake reason bitfield
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2020-10-05 Turn off Velocity Filter unless swinging hammer. Running the velocity filter in the ADC interrupt caused issues with reading lidar from its serial port.
    [hammerController.cpp]
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2020-10-18 Update TODO.md
    Confirmed by Russel on 10/17 via slack that the UART8 can be used instead of UART 6 so the removed change is no longer needed.
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2021-04-30 Updating PDF and Altium docs so that beaglepin -> FET is mapped accurately.
    [FET.SchDoc, Main.PcbDoc, Main.SchDoc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]
